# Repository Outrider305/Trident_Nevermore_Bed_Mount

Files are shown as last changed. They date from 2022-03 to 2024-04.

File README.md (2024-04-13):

# Trident_Nevermore_Bed_Mount

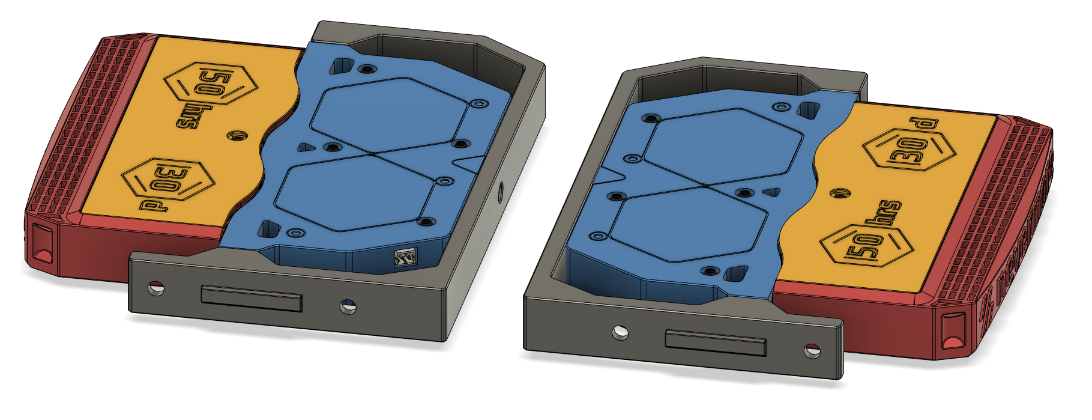
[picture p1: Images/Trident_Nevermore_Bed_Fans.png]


Total redesign of my original Nevermore Spacer Mount for Voron Tridents. This version utilizes it's own modded V5 Duo plenum and cartridges with a third set of magnets. I found that any slight bump or the occasional z-hop with the original parts would cause a cartridge loaded with carbon to fall off the plenum. Hopefully the added magents will solve that problem.

## Long-term use findings.

It's been about one year since I updated this mod and I've learned more about airflow and carbon filtration since then. As such, here are my findings and last update:

- This mod does not do well in toasty chamber temps. My Trident settles around 68C+, and after a year, the brackets and the nevermores have severely warped.
- ABS/ASA still warped even though I have kinematic bed mounts, so the nevermores were farther away from the bed than most Tridents.
- If you still want to print this mod, I recommend any material that has a higher temp rating than ABS/ASA.
- Regular carbon does not do well over 60C chamber temp, so this mod would require 100% use of Nevermore Scortch pellets or a generic substitute.
- Fulling loading the charcoal basket severely cuts down on air flow.
- There are better methods for both VOC filtering and bed fans. Experimenting with this mod was fun while it lasted.

## Version 1 and 2 Comparison

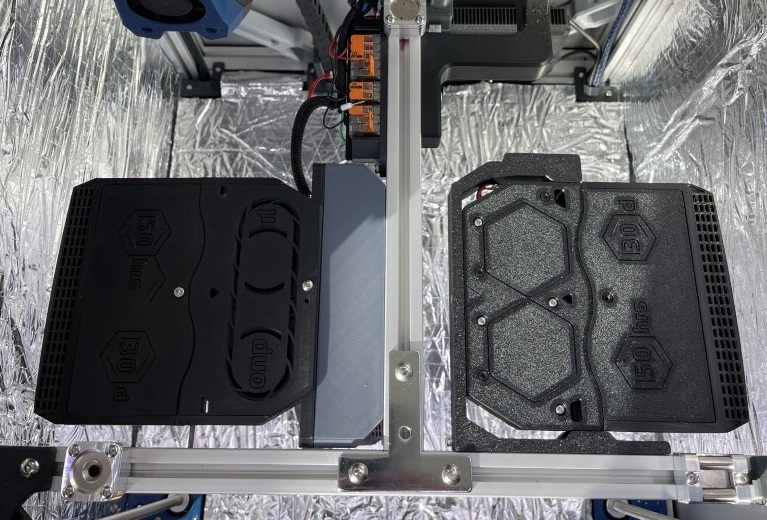
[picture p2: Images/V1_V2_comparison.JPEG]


## New Version Features

Intake orientation for the Nevermore has been inverted to draw cooler air from below the bed. This will help extend the use life of the carbon,<a href="https://discord.com/channels/1017933489779245137/1018610421311225966/1036338929097523210"> per this post on the Nevermore Discord. </a>

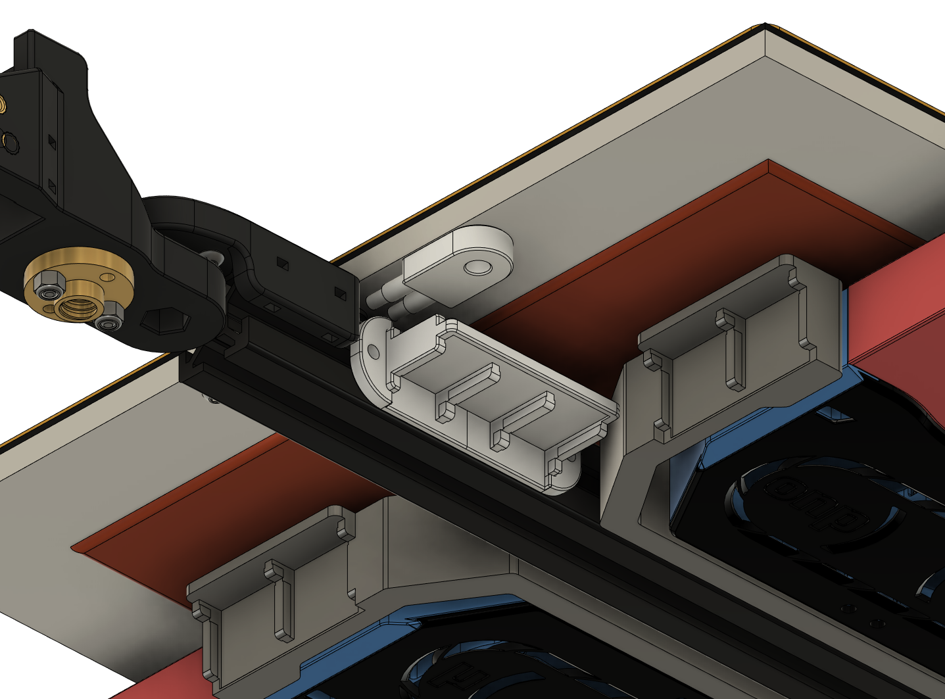
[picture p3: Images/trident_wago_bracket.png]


There is also now one mounting bracket for all Trident sizes and will reduce filament usage for larger Trident owners. The bracket includes mounting points for 3-slot Wago 221s to power the nevermores. Details below on how I powered my nevermores. I've included a Wago mount for regular Trident bed power connections. I've also left my older large Wago mount with space for extra 24V mods.

## Change Log

- **03/15/2023**
	- Moved revised bracket mount out of experimental into main STL folder. Removed previous version.
	- Fixed clearance issue with plenum lid.
- **02-19-2023**
	- Added new untested bracket to Experimental folder in STLs. New bracket has improved M5 mounting points and replaces the single M3x8 screw with M3x12.
- **11-28-2022**
	- Updated Plenum body STL. Removed chamfer on M3 holes for 5015 screws and replaced with crosshatch bridging.
	- CAD updated.
- **11-24-2022**
	- Updated brackets to use BOM standard M5x10 screws rather than M5x8.
	- Adjusted geometry of built-in support for cartridge heatset insert. Should be easier to remove with pliers.
	- CAD updated.
	
## Recommended Print Settings and Material

- Standard Voron part settings (4 walls, 5 top and bottom layers, 40% infill)
- <s> ABS or ASA recommended for this mod. </s> **If you want to print this mod, you need something more heat resistant than ABS/ASA.** 

## BOM (per Nevermore)

- M5x10 screws x2

- M5 roll-in t-nut/hammerhead nut x2

- M3x5x4 (Standard Voron size) Heatset Inserts x7 

- M3x12 screws x3

- M3x16 x4

- 3-slot Wago 221s x2

- 24 AWG wiring

## Assembly and Installation - WIP

**Removal of Trident bed is recommended for easier access.**

1. Install and wire 5015 fans in the plenum according to your preference. If using JST XH connectors, it must be connected before mounting the plenum on the bracket. There will not be enough space to run wiring or connect JST after mounting nevermore onto bracket.

2. Glue magnets in place on both plenum and cartridge bodies. **VERY IMPORTANT: Do not press magnets in too far. Make sure magnets are flush Pushing magnet in too far will create a weak connection.**

3. Insert M3 heatset inserts on sides of the mounting bracket, at the rear of plenum body, and one in the cartridge. Print-in-place support under the cartridge heatset can be removed with pliers. 

4. Install 3-slot Wagos onto bracket (if you will use them).

5. Mount Plenum onto bracket using M3x12 screws.

5. Mount bracket onto Trident bed extrusion with M5 screws, but don't fully tighten them. You will need to adjust bracket position according to your bed size and cartridge size.

6. Once you have found your ideal bracket position, tighten M5 screws.

7. Run additional 24V+ and 24V- wires through the Z chain to the Nevermore wagos. Details below.

## Power

I wired my nevermores in parallel with +24V power straight from the PSU to the bed wago and a single -24V signal wire from the MCU to a wago which controls both Nevermores. This method reduces the amount of added wires to the Trident bed chain.

Trident_Bed_Wago_Large:
- Top Row
	- 5 slot wago: 24V+ power from PSU
	- 2 slot wago: 24V- signal wire for any other 24V mod.
	- 3 slot wago: 24V- signal wire for Nevermore Bed Fans
- Bottom Row
	- 2 slot wagos for Mains (L/N/G), thermal fuse, and bed thermistor
	
Trident_Bed_Wago_Small:
- Mains L/N/G
- Thermal Fuse
- Bed Thermistor

## Macro Control

<a href="https://github.com/VoronDesign/VoronUsers/tree/master/printer_mods/Ellis/Bed_Fans"> Ellis Bed Fans macros </a>

## Credits

- Thanks to 0ndsk4 and eduncan911 for advice and supporting mods to the Nevermore Micro.
- Inspired by <a href="https://github.com/nevermore3d/Nevermore_Micro/tree/master/V5_Duo/Mods/Rear-Backmount-Plenum_by-mvieleers"> mvieleer's rear backmount nevermore plenum mod.</a>
- Created using original <a href="https://github.com/nevermore3d/Nevermore_Micro"> Nevermore Micro V5 Duo CAD.
- Trident CAD parts imported from the <a href="https://github.com/VoronDesign/Voron-Trident"> official Voron github.</a>

## Contact

Contact me via Discord, outrider305#4587.

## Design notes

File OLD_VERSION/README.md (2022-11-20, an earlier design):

# Nevermore_Spacer_Mount

# If you're thinking about printing this, version 2 is coming in the next few days. The new version will require less filament to print and will have a universal mounting design that fits any Trident size.

Spacer made for mounting <a href="https://github.com/nevermore3d/Nevermore_Micro/tree/master/V5_Duo/Mods/Rear-Backmount-Plenum_by-mvieleers"> mvieleer's rear backmount nevermore plenum mod</a> to the Voron Trident's bed carriage.

Currently optimized for regular v5 Nevermore cartridges. Using XL Nevermore cartridges requires 10mm more clearance. Check spacing before using XL cartridges.

I have only printed the 300 version. The 250 and 350 versions are currently untested. Feedback on those parts is appreciated.

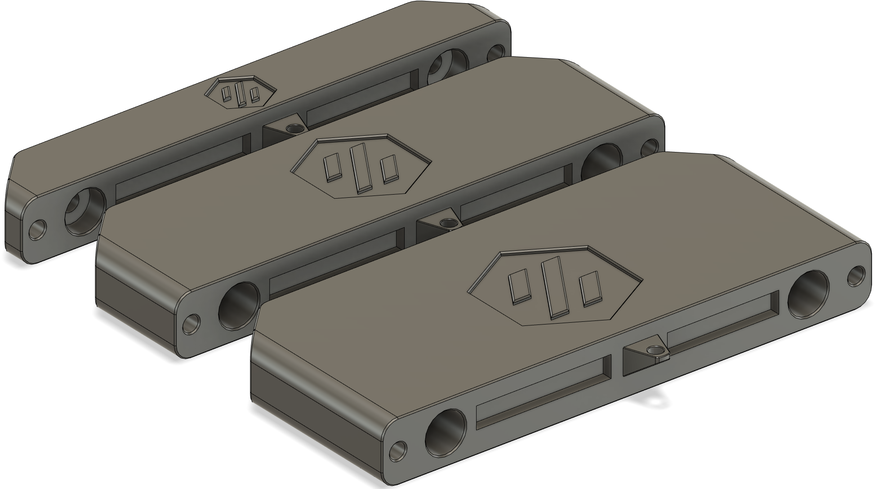
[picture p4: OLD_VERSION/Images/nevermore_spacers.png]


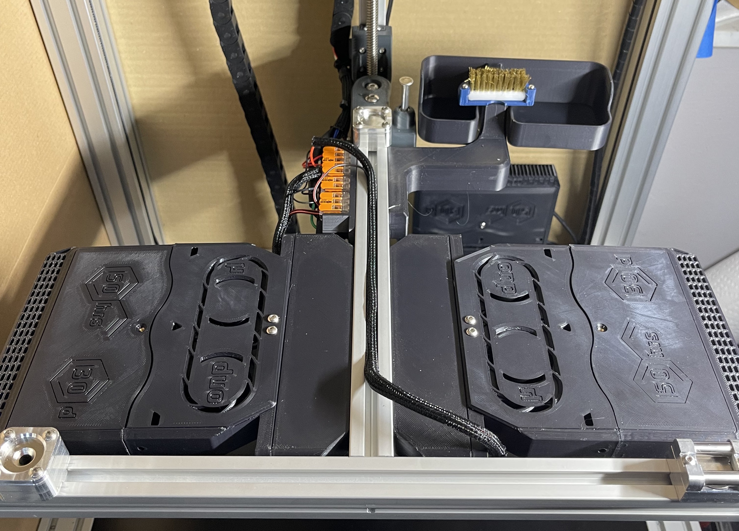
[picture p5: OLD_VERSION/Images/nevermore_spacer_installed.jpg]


Based on the <a href="https://github.com/nevermore3d/Nevermore_Micro"> original Nevermore CAD.</a>

## BOM (per spacer)

M5x35 screws x2

M5 roll-in t-nut x2

M3x5x4 Heatset Inserts x2 

M3x8 screws x2

M3x25 screws x1

M3 roll-in t-nut x1

## Assembly

1. Use soldering iron to install M3 heat inserts.

2. Install M5 t-nuts into Trident carriage extrusion on Y axis.

3. Install M3 roll-in nut into Trident carriage extrusion on X axis.

4. Install Spacer using M5 screws.

5. Insert M3x25 screw into Nevermore plenum side mounting point.

6. Install Nevermore plenum onto spacer, but don't fully tighten M3x8 screws.

7. Partially thread M3x25 screw into roll-in nut. <a href="https://github.com/Outrider305/Nevermore_Spacer_Mount/blob/main/Images/nevermore_side_mount_screw.png"> See photo for example</a>

8. Check alignment of Nevermore with extrusion, and fully tighten M3 screws.

## Power

I powered my nevermores with a common 24V power straight from the PSU in order to reduce the number of wires added to the Z chain. I then ran a single signal cable from the MCU to a wago which triggers all four nevermores. I've included my bed wago mount in the repo.

Trident Power Wago STL:
- Top Row
	- 5 slot wago: 24V+ power from PSU
	- 2 slot wago: 24V- signal wire for under bed LED lights
	- 3 slot wago: 24V- signal wire for Nevermore Bed Fans
- Bottom Row
	- 2 slot wagos for Mains (L/N/G), thermal fuse, and bed thermistor

## Macro Control

<a href="https://github.com/VoronDesign/VoronUsers/tree/master/printer_mods/Ellis/Bed_Fans"> Ellis Bed Fans macros </a>

## Thanks

- Thanks to Chanders on the Voron Discord for feedback and picture of the spacer.

## Contact

Contact me via Discord, outrider305#4587, with any questions.

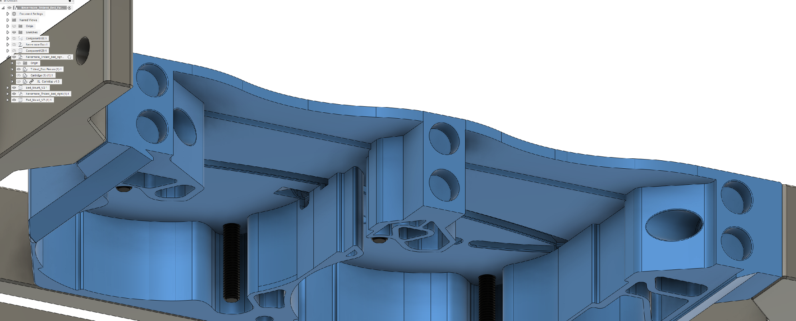
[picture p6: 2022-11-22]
Images/trident_nevermore_magnets.png

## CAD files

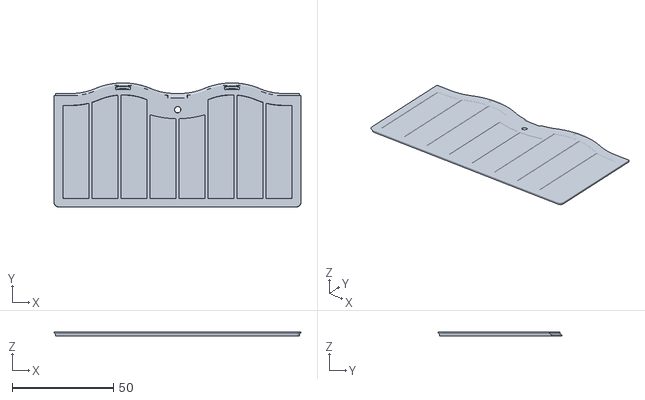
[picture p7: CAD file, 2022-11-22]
STLs/Cartridges/Trident_Bed_Mount_XL_Cartridge_LID.stl
122.0 x 61.3 x 1.78

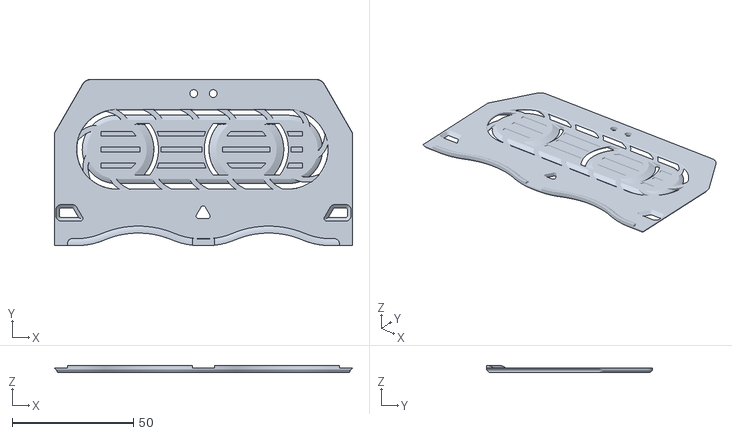
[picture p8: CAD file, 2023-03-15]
STLs/Plenum/Trident_Bed_Mount_Plenum_Lid_r1.stl
122.8 x 68.5 x 2.80

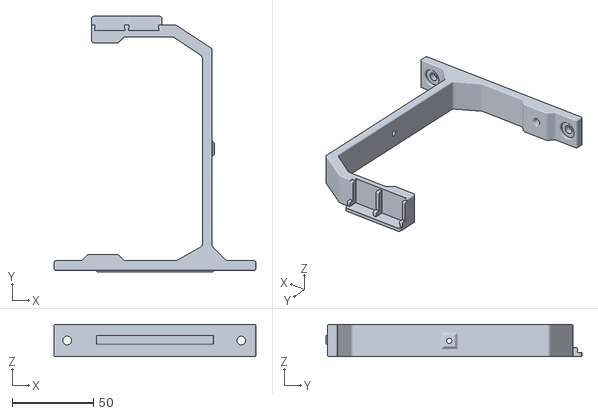
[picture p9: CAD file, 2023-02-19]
STLs/trident_bed_mount_bracket_right_r1.stl
124.4 x 157.9 x 20.0

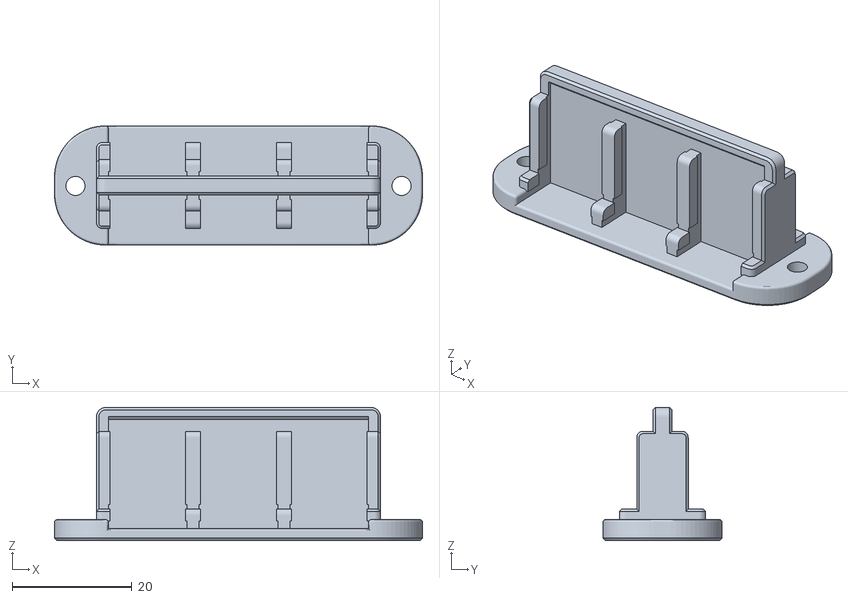
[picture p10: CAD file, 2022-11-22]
STLs/Wago_Mounts/Trident_Bed_Wago_Small.stl
61.5 x 19.9 x 22.2

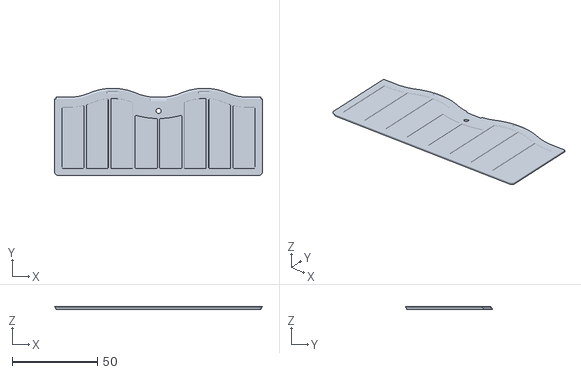
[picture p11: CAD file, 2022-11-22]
STLs/Cartridges/Trident_Bed_Mount_Cartridge_LID.stl
122.0 x 51.2 x 1.78

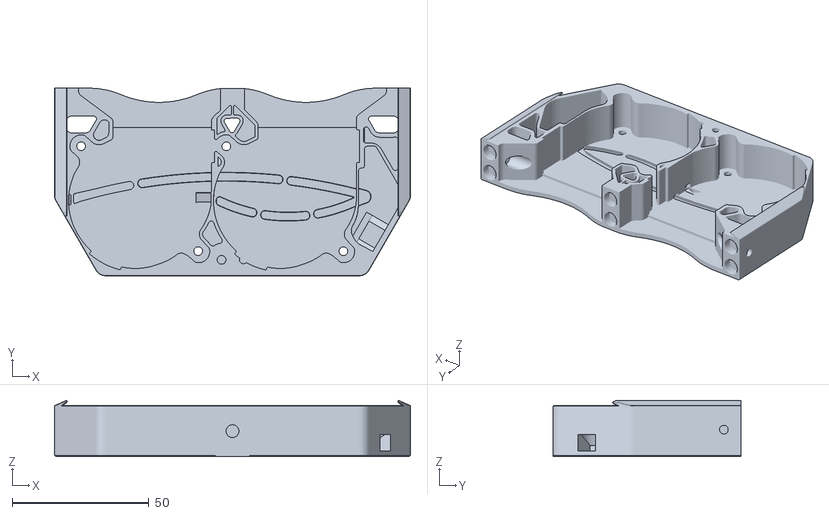
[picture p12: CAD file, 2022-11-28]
STLs/Plenum/Trident_Bed_Mount_Plenum.stl
130.0 x 68.6 x 20.5

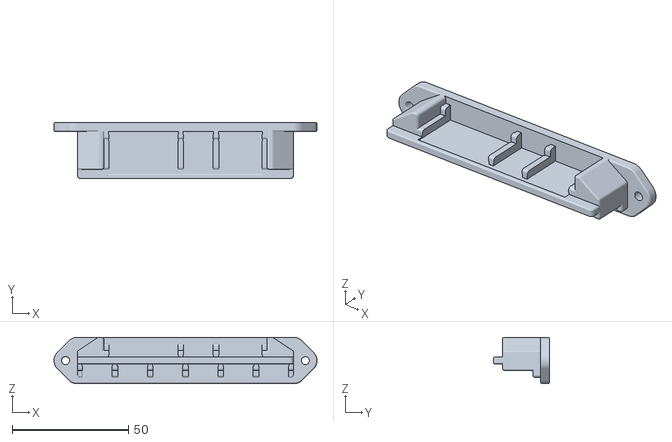
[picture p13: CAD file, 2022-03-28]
STLs/Wago_Mounts/Trident_Bed_Wago_Large.stl
112.9 x 24.2 x 19.9

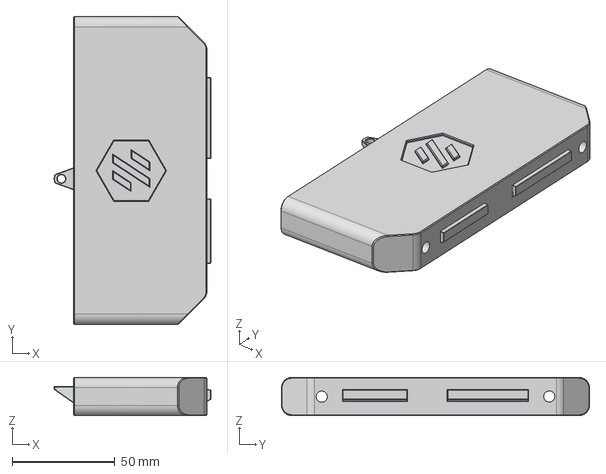
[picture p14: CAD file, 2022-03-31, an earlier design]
OLD_VERSION/CAD/nevermore_spacer v13.step
76.3 x 150.0 x 18.6 mm

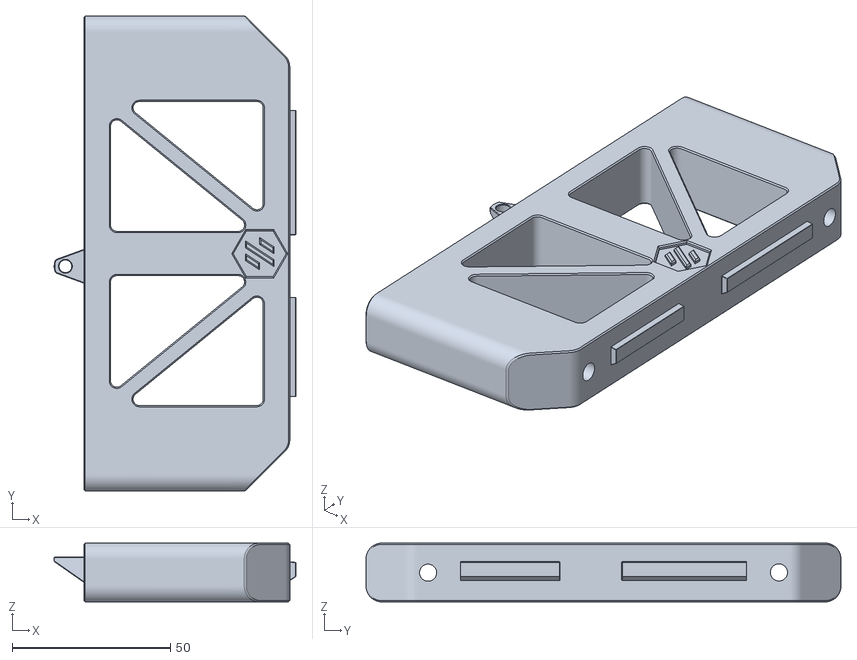
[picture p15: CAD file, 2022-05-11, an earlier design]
OLD_VERSION/STLs/Nevermore_Spacer_350_LW.stl
76.3 x 150.0 x 18.6

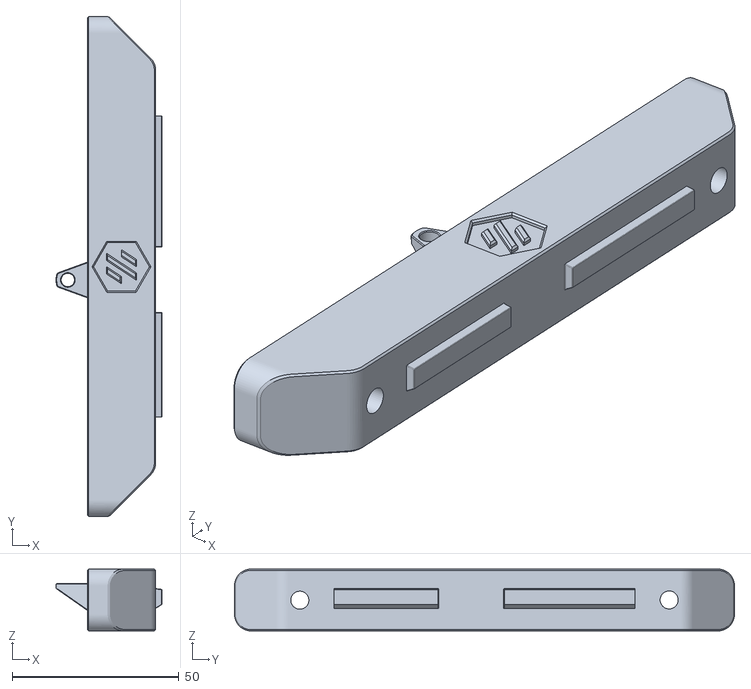
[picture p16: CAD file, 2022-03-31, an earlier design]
OLD_VERSION/STLs/Nevermore_Spacer_250.stl
31.8 x 150.0 x 18.6

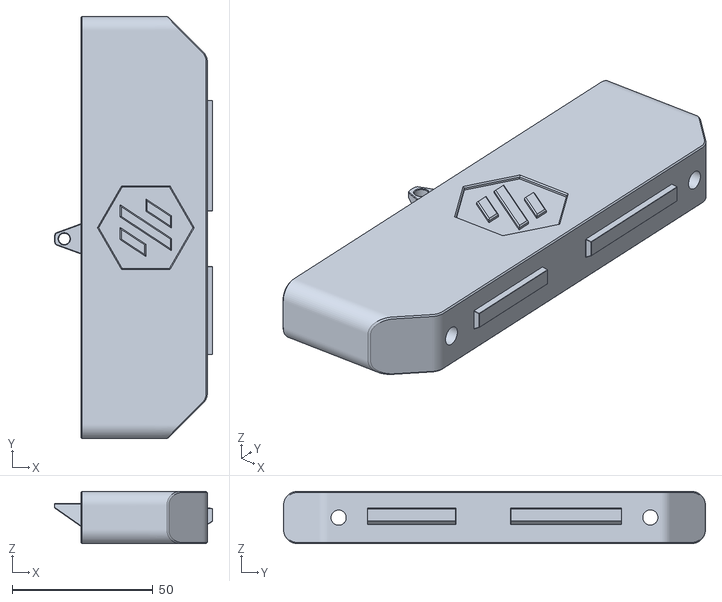
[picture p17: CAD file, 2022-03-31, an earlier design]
OLD_VERSION/STLs/Nevermore_Spacer_300.stl
56.3 x 150.0 x 18.6

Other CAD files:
STLs/trident_bed_mount_bracket_left_r1.stl
OLD_VERSION/STLs/Nevermore_Spacer_350.stl
OLD_VERSION/CAD/nevermore_spacer v13.f3d

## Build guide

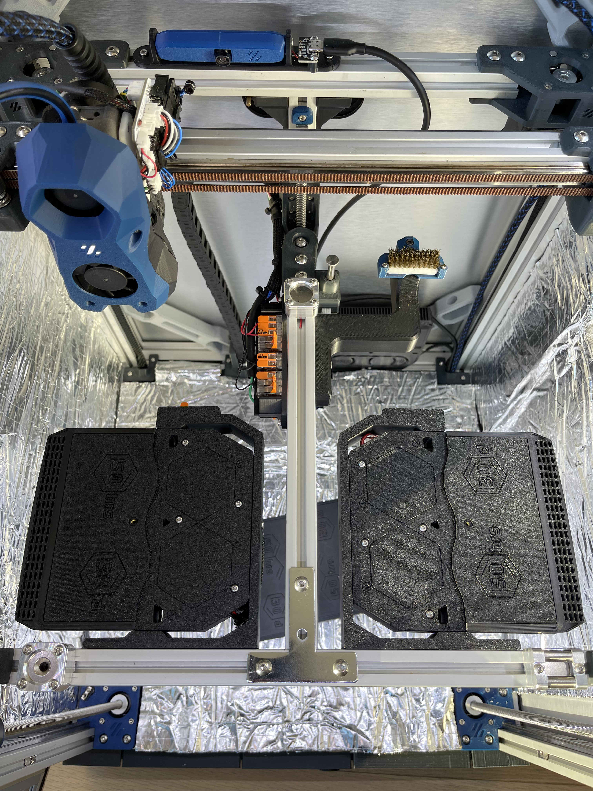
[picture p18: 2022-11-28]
Images/Final_Install.JPEG

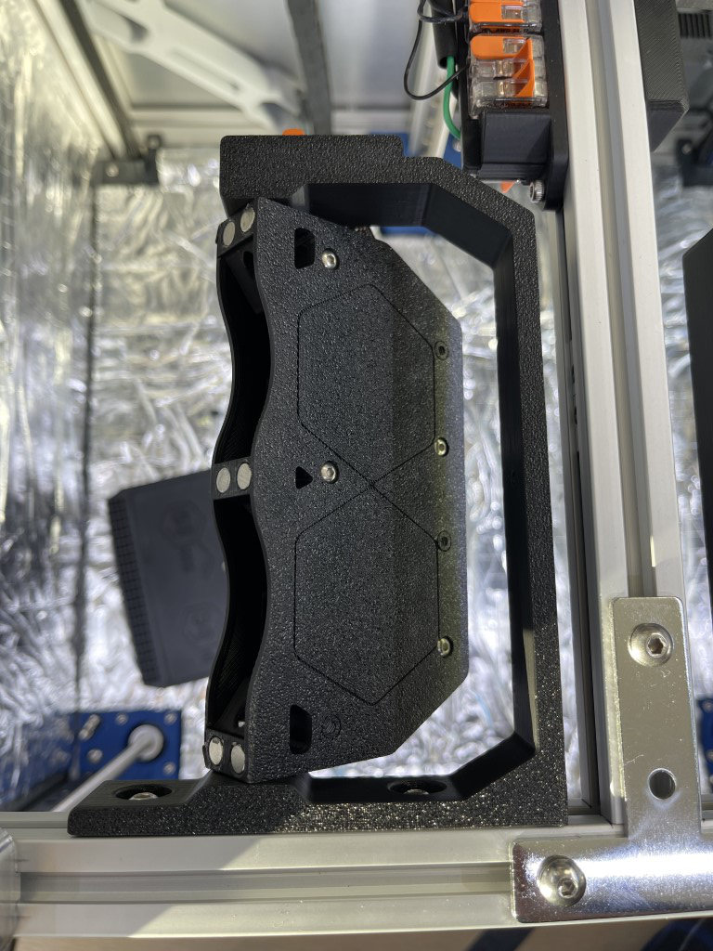
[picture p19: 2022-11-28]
Images/Install_procedure.JPEG

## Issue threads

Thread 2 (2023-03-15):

Cover issue - notch or cut is missing

blonestar, 2023-03-15:
Hey,
I found small issue with a fan cover, the place in the middle missing a cutout or a notch to be able to fit properly.
I've had to cut that with a knife, a scalpel. Now it fits. :)
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

Did not mount it yet but thank you for the mod. :)

Outrider305, 2023-03-15:
Thanks for the heads up! Didn't realize there was a conflict, but I've been using the nevermores with that little lip still there without a problem. I've uploaded a revised plenum lid.

blonestar, 2023-03-15:
Np. I've realized when I've put both nvrm sides on the table and one side was a bit higher.
Also I didn't have time to do that in CAD myself and I already printed same thing twice.
But thank you for quick fix and reply. :)

Closed 2023-03-15.

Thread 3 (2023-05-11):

Plenum lid heatset insert cutout

btoconnor, 2023-05-11:
Thanks for this mod. Getting ready to install it on my Trident.

I noticed when putting in the M3 heatset inserts into the parts last night, that the heatset insert space on the Plenum to secure the lid seemed like it was mis-shaped.  The heatset insert didn't "seat" properly into the hole, and there didn't seem to be enough room for the plastic to settle when the heatset insert was placed (a little sloppily, admittedly, because it was harder to do).

This resulted in a noticeable lip in displaced plastic above the heatset insert that I'll have to cut away, and the M3x16 won't go all the way into the heatset insert (I assume there's plastic stuck in the heatset that I'll drill out)

I'm not sure if this is an issue with my print (though none of the other holes on any of the parts had any issues), the base Nevermore project, this mod, or just random bad luck but figured I'd open the issue.

Here's a picture of the part as it stands before any drilling / cutting - the screw is in as far as I can insert it by hand:
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

btoconnor, 2023-05-11:
I downloaded the f3z file and was able to look at it a little more closely (should have done that first I guess - pretty new to all of this)

It looks like the heatset insert hole diameter for the cartridge is 4.7mm - this one fit fine with zero issues.
The hole for the plenum heatset insert is showing as 3.2mm - which I think would explain the issue here.

I haven't gotten a chance to go through the CAD files for the nevermore base project, and I'm not sure how much of these objects are just slightly tweaked vs redesigns.

btoconnor, 2023-05-11:
Okay - I think I might have an idea what happened. I opened the f3z file for the Nevermore project's plenum, and the hole in question here is 3.2mm.  However - it seems that it's a passthrough hole to a heatset insert that sits below it.  In this project (since it's being mounted to the arm, and doesn't need that cutout), that opening does not exist for the heatset insert to pass through to:

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

I think that simply making this hole on the plenum in this project to 4.7mm should solve the issue described.  I did a quick hack job here to expand it to 4.7mm and I'll try and print it out today and see if it resolves my issue.

Definitely let me know if I'm misunderstanding something fundamental though!

btoconnor, 2023-05-12:
Update: I printed out the plenum with the heatset insert for the lid at 4.7mm rather than 3.2mm and it works perfectly.  I'd be happy to submit a PR, but I'm not so great with CAD and I don't think I'd be able to sufficiently commit the change back to the f3z file since importing it seemed like it didn't contain any of the original sequence.  Let me know if and how this should be continued if desired.

Thanks again for creating this mod!

Outrider305, 2023-10-04:
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

Hey. I'm so sorry I didn't see your messages earlier. I took a long break from 3d printing and I'm just getting back into it.

So I removed that headset in the triangular cutout from the plenum. That heatset is meant to retain the vertical mounting point from the original nevermore v5. I replaced that heatset location with the 4.7mm hole on the outside of the plenum. It's meant to secure the plenum to the bracket.

The 3.2mm hole that you put a heatset insert into is for the screw that retains the lid, but it doesn't take a heatset insert. The lid screw just threads into bare plastic.

Closed 2024-04-09.

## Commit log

2022-03-28 Add files via upload
    Bed Wago mount to hold Wago 221s for:
    - Bed AC Line
    - Thermal Fuse
    - Bed Neutral
    - Bed Ground
    - Thermistor
    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
    [Trident Combined Power Wago (1).stl]
2022-03-28 updated repo
    [Neveremore_Spacer_300.stl, Trident Combined Power Wago (1).stl, Trident Combined Power Wago.stl]
2022-03-31 CAD and STL updates
    [Neveremore_Spacer_300.stl, Nevermore_Spacer_250.stl, Nevermore_Spacer_300.stl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]
2022-03-31 350 spacer update
    [Nevermore_Spacer_350.stl]
2022-11-22 STLs added
    [Trident_Bed_Fan_Bracket_Left.stl, Trident_Bed_Fan_Bracket_Right.stl, Trident_Bed_Fan_Cartridge_LID.stl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]
2022-11-28 Plenum update
    [Trident_Bed_Fan_Plenum.stl]
2022-11-28 Plenum STL fix
    [Trident_Bed_Fan_Plenum.stl]
2022-12-02 Files renamed
    [Trident_Bed_Mount_Bracket_Left.stl, Trident_Bed_Mount_Bracket_Right.stl, Trident_Bed_Mount_Cartridge_LID.stl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]
2023-02-19 bracket revision
    [bed_mount_bracket_left_r1.stl, bed_mount_bracket_right_r1.stl]
2023-03-15 Bracket and Plenum Lid revisions
    [Trident_Bed_Mount_Bracket_Left.stl, Trident_Bed_Mount_Bracket_Right.stl, Trident_Bed_Mount_Plenum_LID.stl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]
